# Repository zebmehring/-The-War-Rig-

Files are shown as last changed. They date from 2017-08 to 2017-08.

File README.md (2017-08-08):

# -The-War-Rig-

These are the SolidWorks design files and other submitted material for a project in Yale's Undergraduate Mechanical Engineering program (specifically for MENG 185 - Mechanical Design). The project was completed over the course of spring 2016. All files are posted here under fair use and all credit for the assignment and associated administrative files goes to the issuing department.

* tl;dr: I helped build a remote controlled car out of stuff you really shouldn't bother building a remote controlled car out of. But it drove pretty ok, I guess.

The goal of the project was to construct a remote-controlled vehicle using laser-cut delrin, aluminum rod, plastic gears, toy-car-like-tires, and 3 motors from power screwdrivers. It underwent testing on an obstacle course that involved: pulling a 7kg block of lead up a 45 degree slope, navigating over rough terrain, traversing through a tunnel, making a tight turn, and weaving through a set of cones. Thus, the specifications of dimension, manuverability, and power were had to be optimized for. For example, plenty of torque could be achieved with the maximum number of motors and gears, but this constrained the vehicle in other capacities. Materials were a constrained variable--a specified budget for gears, number of motors and wheels, and supply of rod and delrin could be used in the final design. Calculations were done to ensure correct gear ratio for proper torque, ideal dimensions for combating obstacles, and other variables.

Overall the project was a success--"The War Rig" was able to complete all obstacles save the block towing (this specification was later concluded to be unfair for the power of the motors which were given in the year the experiment was conducted--even with 3 forward-facing motors and optimal gear ratios, this was a challenging feat). It came out second overall in terms of raw performance in the class.

My personal contributions include: designing the chassis to maximize stability while conforming to dimensional constraints (yes it looks goofy, but it works!), designing external set of chassis walls to protect the gear train and stabilize the axles (taking the vehicle from immobile to driving), testing the power of the motors and calculating the appropriate gear ratios to achieve estimated power, much machining and finagling to get parts to fit together, and writing the majority of the final report.

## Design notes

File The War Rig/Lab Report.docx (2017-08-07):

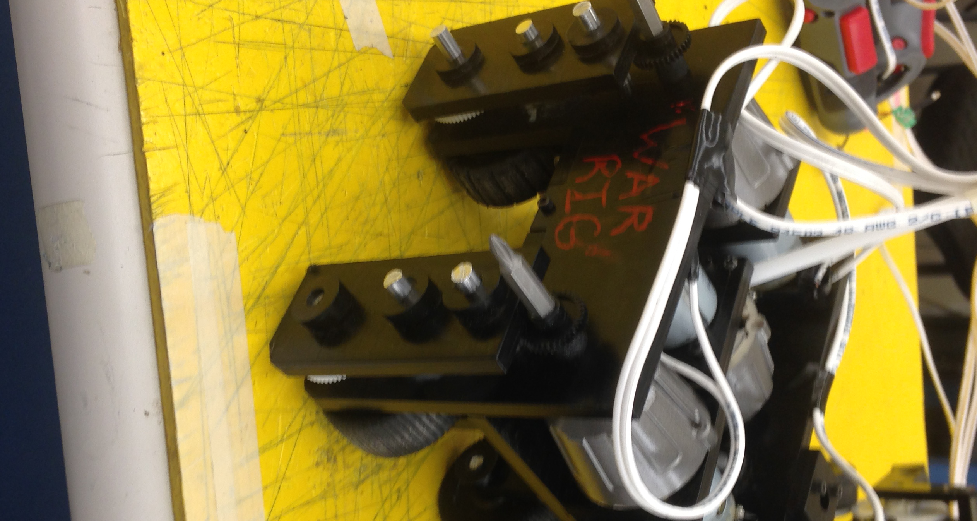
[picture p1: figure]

Lab #3 – ATV

T1—“War Rig”

Sierra Jackson, Stuart Monk, Zeb Mehring

MENG 185: Mechanical Design

10 May 2016

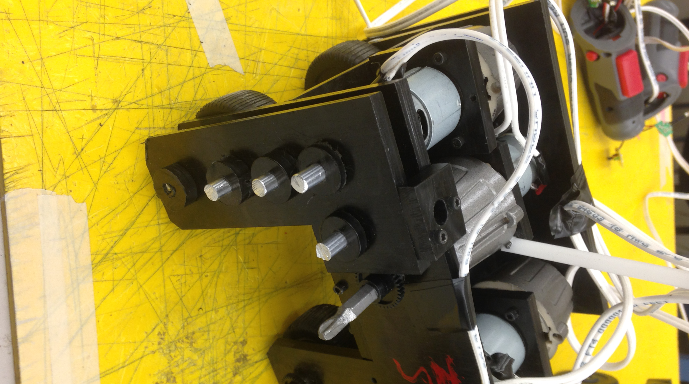
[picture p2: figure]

Overview:

The ultimate objective of this lab was to build an ATV capable of traversing a pre-specified obstacle course. To construct it, we were given three power screwdrivers, a sheet of Delrin (equivalent to 12x12” in surface area), three feet of a .25” diameter aluminum rod, wheels, screws, and $80 with which to purchase plastic gears.

Our approach was to create a three-wheeled vehicle driven by all three motors from the power screwdrivers. The steering is differential: it is accomplished by modulating the turning of the front motors by the driver. The gear ratio was calculated based off of the estimated necessary torque increase, and idle gears were added to raise the chassis base and increase the undercarriage clearance. A combination of screws and “puzzle geometry” were used to lock the chassis into place, while axles held between two or three supporting walls served as mounts for the gears and wheels. The wheels were given treads to increase traction and because treads (along with the battle spikes a.k.a. drill bits) look awesome.

The goals for this design were: to create a vehicle that could provide a high torque (we erred on the side of completing the course rather than going for record-times), to make a simple steering system that did not rely on the proper operation of a single motor and its gear train, to minimize the total volume occupied by the vehicle to increase the error margin resultant from the driver, and to build a model that would be sturdy enough to withstand multiple bouts of practice and competition. The final product, though it veered from the ideal conceptual design, achieved most of these goals.

Design Specifications:

Specification | Dimension
Mass | 1.8 kg
Undercarriage Clearance | 3.2 cm
Turning Radius | 11.4 cm
Drive Train Gear Ratio | 162 (each of 3 motors)
Steering Gear Ratio | 162
No Load Horizontal Speed | 7.6 cm/s
Peak Power | 20 W
Towing Capacity | 27 N

Evaluation:

Several of our goals were happily exceeded by our car. Our turning radius in practice was phenomenally small, as we did not anticipate being able to drag the rear wheel train without driving it (a feat of which the final product was capable). Our car was also perfectly sized despite the addition of drill bits to mount the pinion gears which increased the width by about an inch. Although ground clearance was a theorized issue, our car managed to overcome every obstacle without noticeable problems. We were able to hitch the trailer and drag it up the modified ramp with ease, and we were also able to drive our vehicle (perhaps better than forwards) backwards.

Certain other goals were not met to our full satisfaction, mostly design (as opposed to performance) related ones. We were never able to fully solve a gear meshing issue on our second motor’s gear train which inhibited the maximum torque our car could produce. Similarly, a strange weight imbalance caused issues with creating enough normal force on that same wheel for ideal torque production. More generally, our design failed to be as simple as we had originally envisioned. With many axles and attachment points, a big flaw in our design turned out to be the need to assemble everything at once (which was very difficult). Furthermore, editing the assembled car was difficult and disheartening because of this fact.

If we were to begin from scratch, we would have optimized our design and assembly processes in several ways. Firstly, we would have designed keeping assembly in mind, to eliminate the problems caused by having to put everything together at once and by having to deconstruct the entire model to repair the motors. We would have also looked for a more precise way to mount our gears to improve meshing. Finally, we would have implemented features like a fourth wheel, the inner wheel mounts, and the motor mounts much earlier on in the process. This being said, our overall design would not be altered significantly.

Process:

We began with an in-class brainstorming session which spawned numerous options for our design—four wheels vs. three wheels, two driving motors vs. three driving motors, shared wheel axles vs. single wheel axles, etc.—but we initially settled on a three-wheeled, three-motor layout. This design was chosen because it was the simplest (in theory), had an uncomplicated steering mechanism, conferred decent agility, and could be compacted into a small space to better traverse the obstacle course.

From this idea, we created a foam core model. It had two steering wheels at the front controlled by two separate motors driving different gear trains of equal gear ratio. The back wheel was placed in a Delrin box which was connected axially to a motor which would allow it to pivot. All three motors were housed laterally in a box-shaped chassis with significant ground clearance.

Upon review and discussion, we modified several aspects of this design to better suit our goals for the project. Because we were advised that the “rudder” pivot wheel would not greatly contribute to the steering of the ATV, we instead converted it into a static wheel driven straight forward by the third motor. This increased our overall torque in exchange for a small advantage in turning (now the differential system would have to overcome the friction of a sliding back wheel). As a result, the back axle became a much simpler system. Also addressed was a stability issue: lack of dual axle support. We added in external support walls to give each axle two bases to balance on and to protect the gears from bumping into the course as a result of reckless driving. Finally, the driving wheels were placed underneath the chassis instead of outside of it, reducing the total width of the vehicle by at least two inches.

Further nuance was added in the CAD phase, which involved creating every part on SolidWorks. Each group member worked on a different part of the vehicle, adding the proper dimensions, shaft holes, and other features based on the measurements taken from the motors and the restrictions imposed by the obstacle course. In addition to our foam core model, we added dovetails to select pieces of the chassis to increase stability and also specified the sites on the design where we wanted to insert screws (by using a quick burst of heat from the laser cutter). We also added motor mounts in this phase to secure the motors to the chassis even more tightly. Each group member then worked on different subassemblies (wheel axles, chassis, gear trains, etc.) until all the constituent pieces were ready to assemble the final design. Mates were quickly added and we cycled through turns creating the final in-context screw holes before submitting the assembly for cutting.

With all the materials in hand, we proceeded to machine and assemble the model. Using the drill press, we tapped all the necessary screw holes. The hacksaw was used to create axle bits of specified length and the bandsaw was used to tread the wheels. The lathe was used to machine the axle caps. As finalized pieces became available, we used the arbor press to press-fit axle caps, gears, and wheels onto their respective shafts, which then became locked to the chassis (occasionally having to drill through the shaft and use small pins to secure the fit). After a complex analysis of which parts to secure first, we proceeded to screw everything into place. Throughout this process, countless subassemblies were made to ensure that the parts interfaced, and many times small corrections had to be made. As a result, it was much less methodical than depicted here.

The tweaking and repair process consisted mainly of: disassembling the car to repair the motors, attempting to increase the weight on the starboard side of the car to give the second wheel traction, screwing on makeshift supports to mesh the second gear train better, and test driving the car to make sure that everything was working harmoniously.

After much toil, the car eventually drove neatly and was able to accomplish many of the goals we had in mind. Coincidentally, these pieces finally came together just before the deadline, so no further attempts to fix non-critical issues were able to be made.

Time Log:

Activity | Person Hours
Conceptual Development | 12
SolidWorks | 18
Milling | 102
Assembly | 30
Repair and Redesign | 24
Evaluation | 4
Total | 190

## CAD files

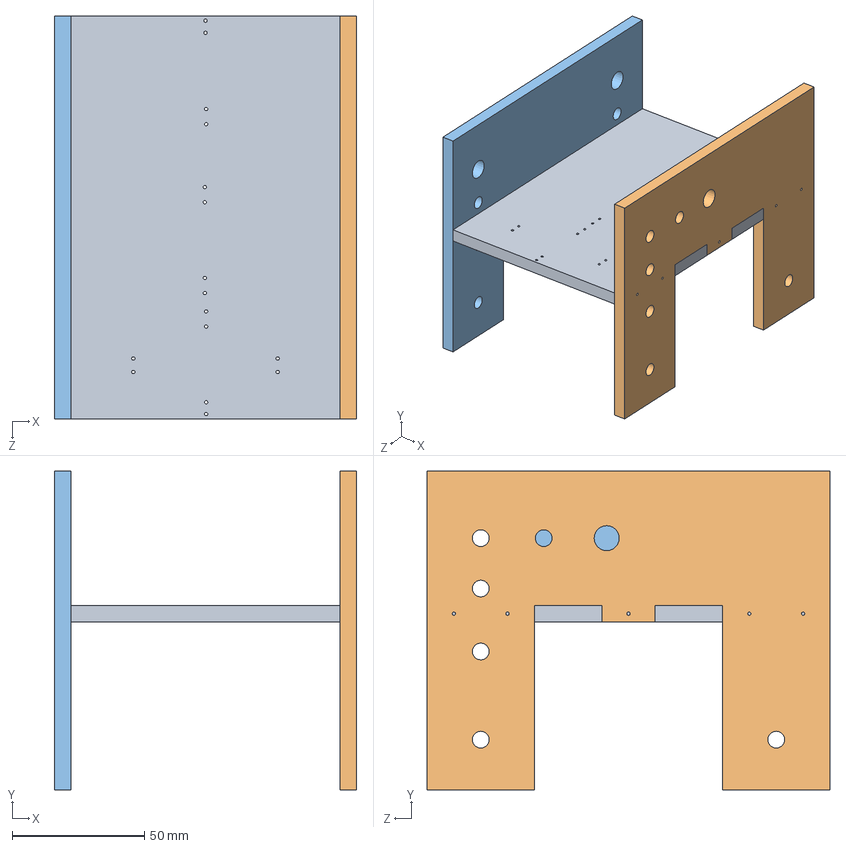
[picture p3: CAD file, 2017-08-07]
The War Rig/Sierra, Stuart, Zeb Car Parts/Assemblies/JMM-Chassis_Assembly.SLDASM
114.3 x 120.7 x 152.4 mm
Base_Plate
Side_Plate (1M)
Side_Plate (2M)

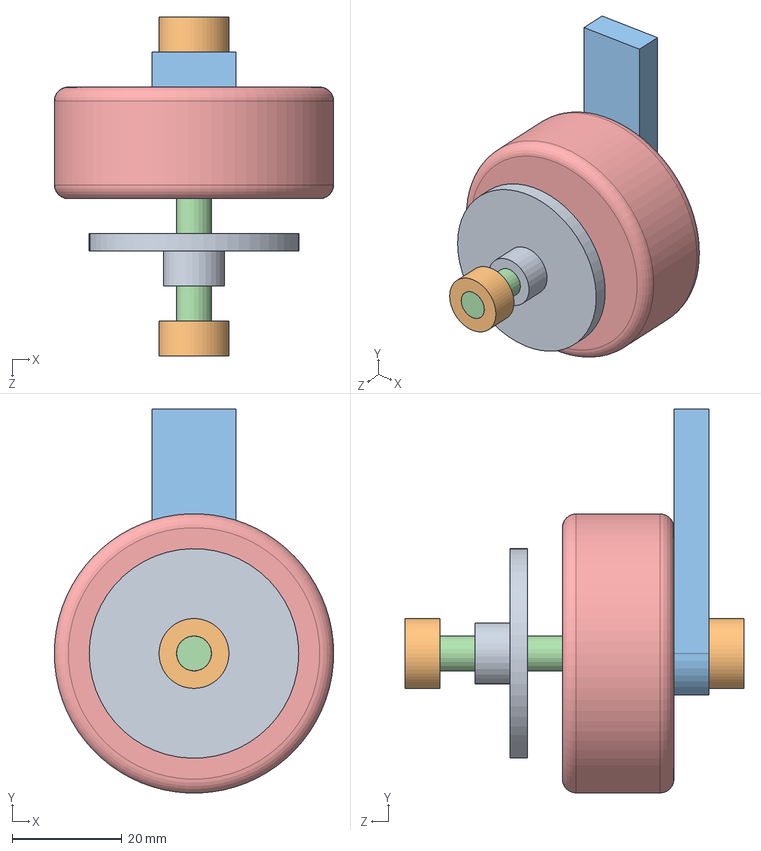
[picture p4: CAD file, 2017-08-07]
The War Rig/Sierra, Stuart, Zeb Car Parts/Assemblies/JMM-Front Wheel Assembly.SLDASM
50.8 x 69.8 x 61.6 mm
72-Gear
Axel Washer x 2
Front Wheel Support
Front Wheels Axel
Wheel

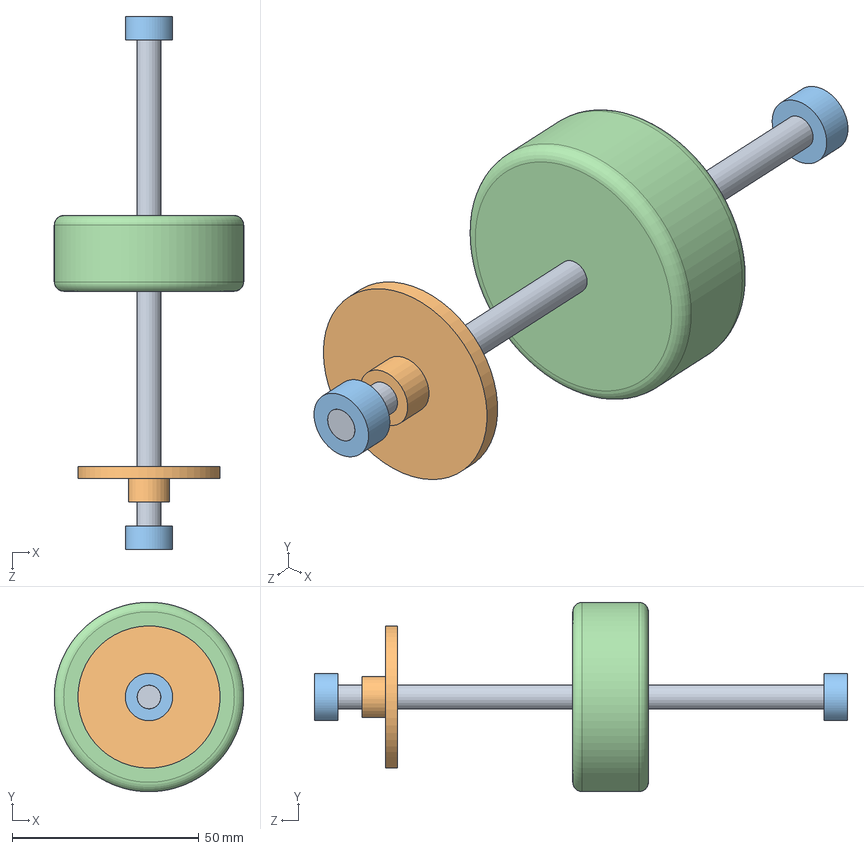
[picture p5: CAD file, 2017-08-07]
The War Rig/Sierra, Stuart, Zeb Car Parts/Assemblies/JMM-Back Wheel Assembly.SLDASM
50.8 x 50.8 x 142.9 mm
Back Axel
72-Gear
Axel Washer x 2
Wheel

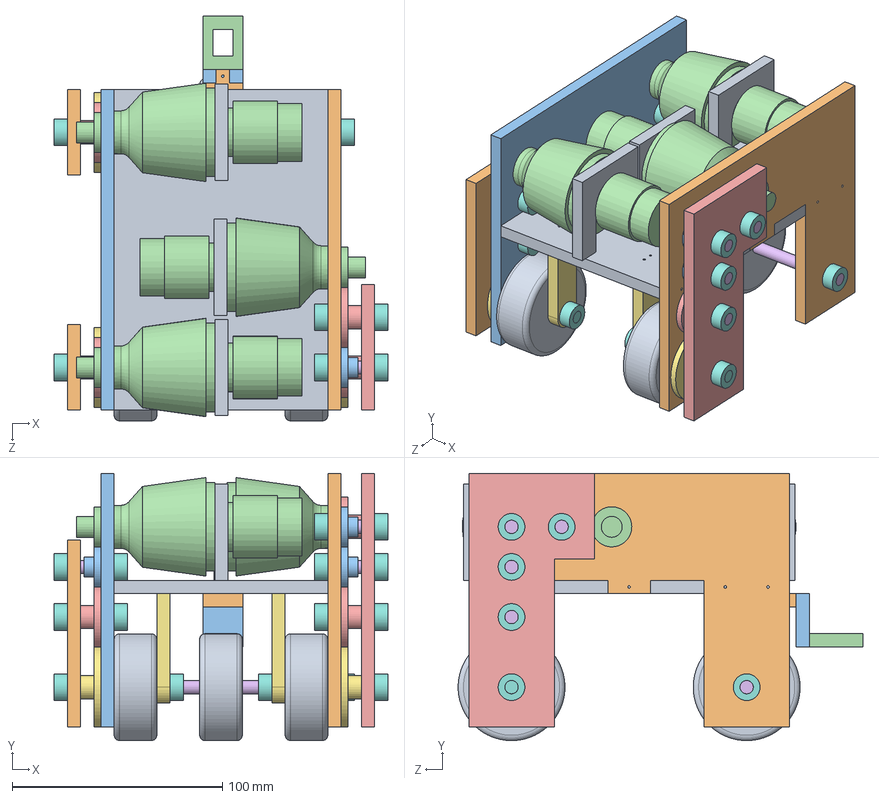
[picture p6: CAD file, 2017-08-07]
The War Rig/Sierra, Stuart, Zeb Car Parts/Assemblies/JMM-Car_Assembly.SLDASM
158.8 x 127.0 x 192.4 mm
Base_Plate
Side_Plate (1M)
Side_Plate (2M)
motor x 3
L_Gear_Cover_Plate
Back Axel
72-Gear x 3
Axel Washer x 22
Wheel x 3
Straight_Gear_Cover_Plate x 2
36-Gear x 4
36-Gear for Engine x 3
54-Gear x 4
Train Axel x 8
Front Wheel Support x 2
Front Wheels Axel x 2
Motor_Support x 3
Trailer_Arm_H
Trailer_Arm_V
Trailer_Hook

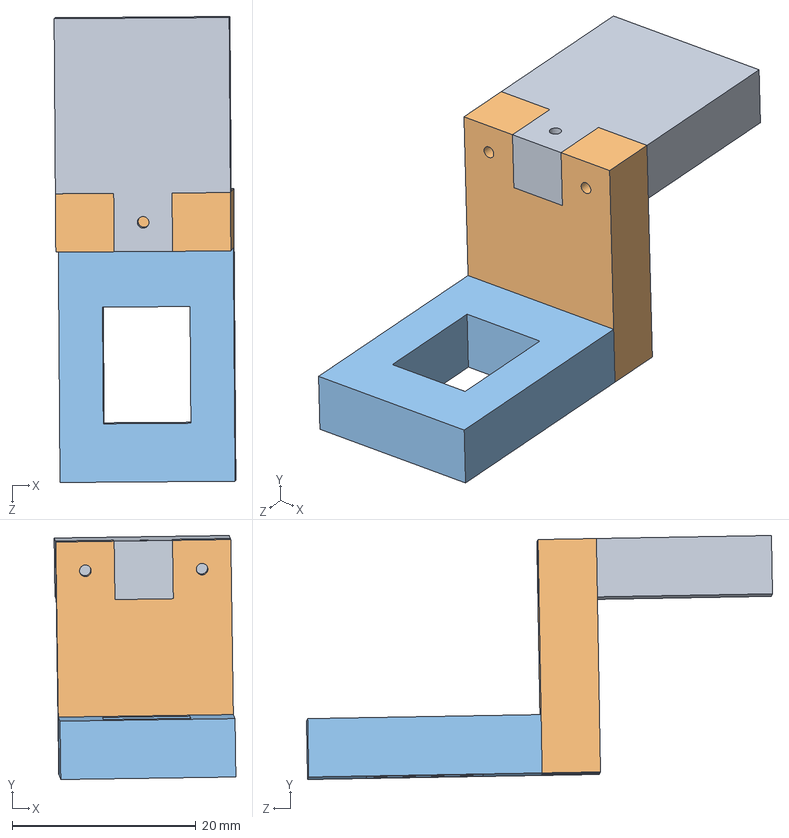
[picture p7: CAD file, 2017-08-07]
The War Rig/Sierra, Stuart, Zeb Car Parts/Assemblies/JMM-Trailer Hitch.SLDASM
19.8 x 26.6 x 50.7 mm
Trailer_Arm_H
Trailer_Arm_V
Trailer_Hook

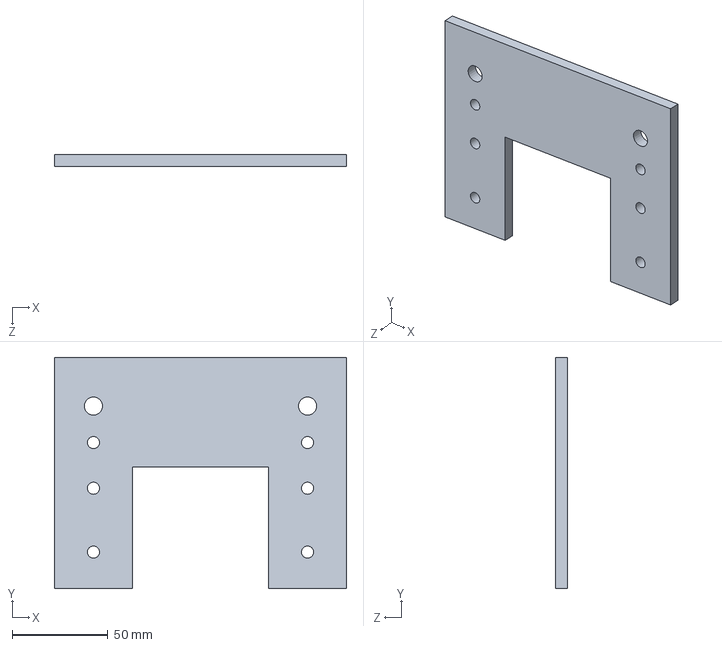
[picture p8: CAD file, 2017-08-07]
The War Rig/Sierra, Stuart, Zeb Car Parts/Parts/JMM-Side Plate (2M).SLDPRT
152.4 x 120.7 x 6.35 mm

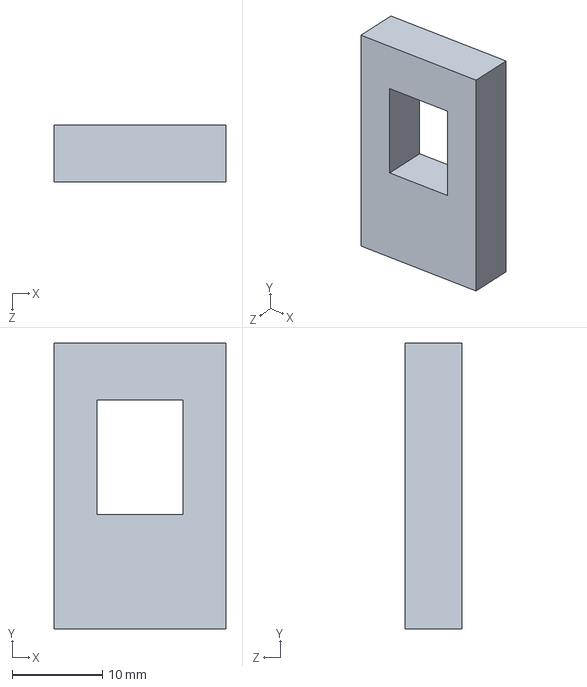
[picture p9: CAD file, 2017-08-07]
The War Rig/Sierra, Stuart, Zeb Car Parts/Parts/JMM-Trailer Hook.SLDPRT
19.1 x 31.8 x 6.35 mm

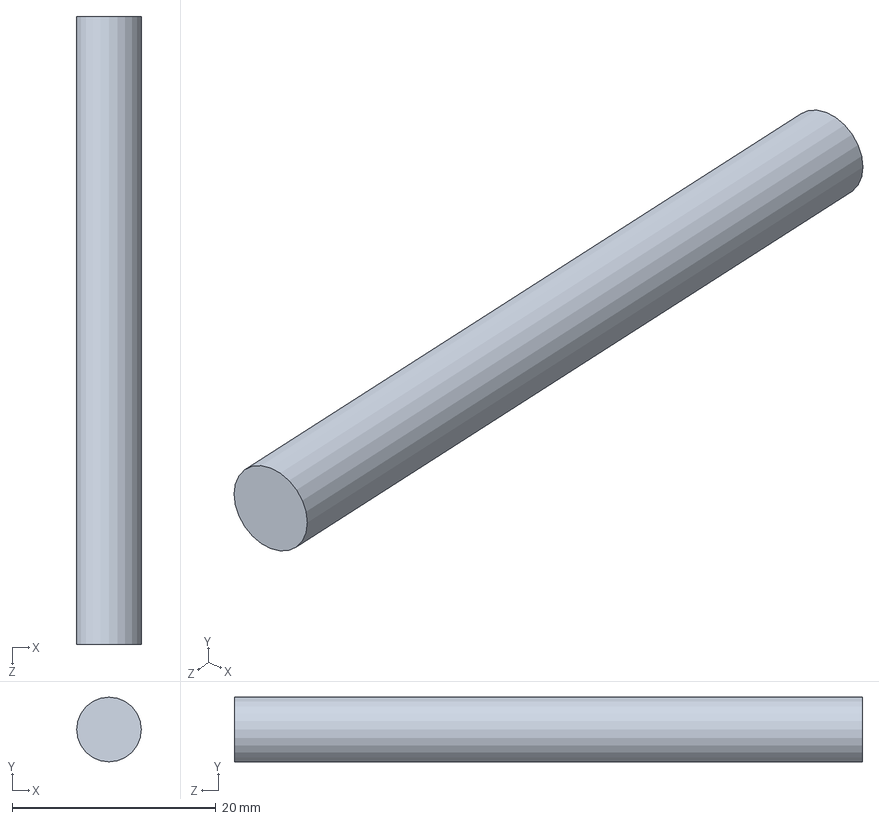
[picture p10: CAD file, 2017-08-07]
The War Rig/Sierra, Stuart, Zeb Car Parts/Parts/JMM-Front Wheels Axel.SLDPRT
6.35 x 6.35 x 61.6 mm

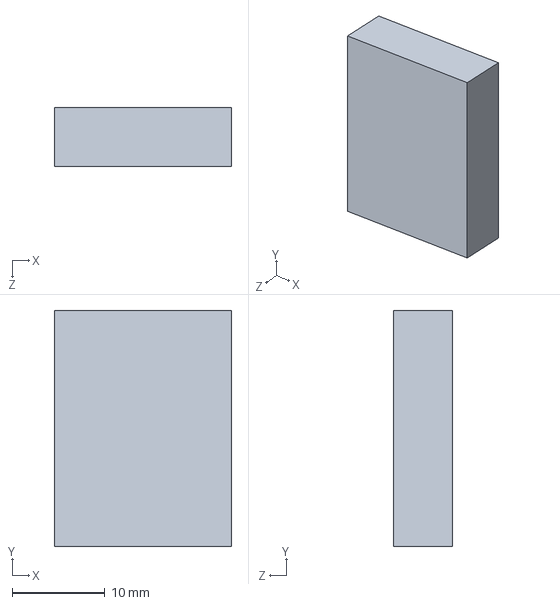
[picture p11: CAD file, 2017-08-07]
The War Rig/Sierra, Stuart, Zeb Car Parts/Parts/JMM-Trailer Arm V.SLDPRT
19.1 x 25.4 x 6.35 mm

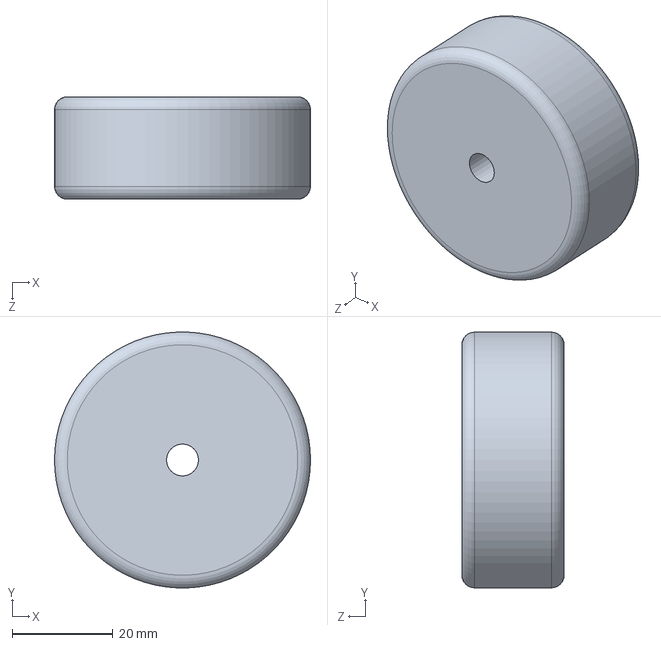
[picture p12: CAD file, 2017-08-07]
The War Rig/Sierra, Stuart, Zeb Car Parts/Parts/JMM-Wheel.SLDPRT
50.8 x 50.8 x 20.3 mm

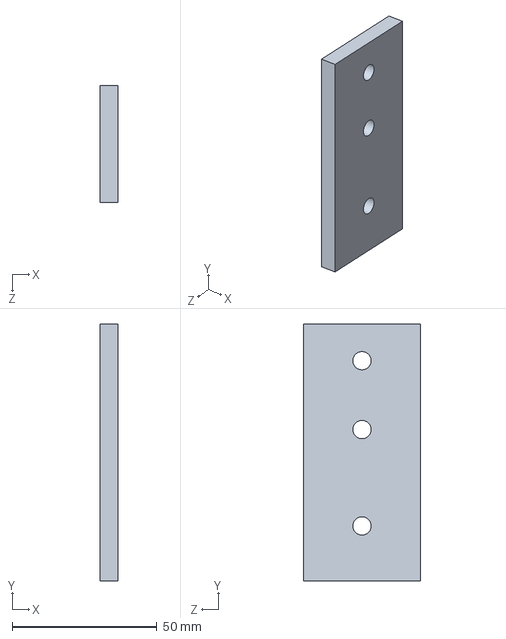
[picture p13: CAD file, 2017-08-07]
The War Rig/Sierra, Stuart, Zeb Car Parts/Parts/JMM-Straight Gear Cover Plate.SLDPRT
6.35 x 88.9 x 40.6 mm

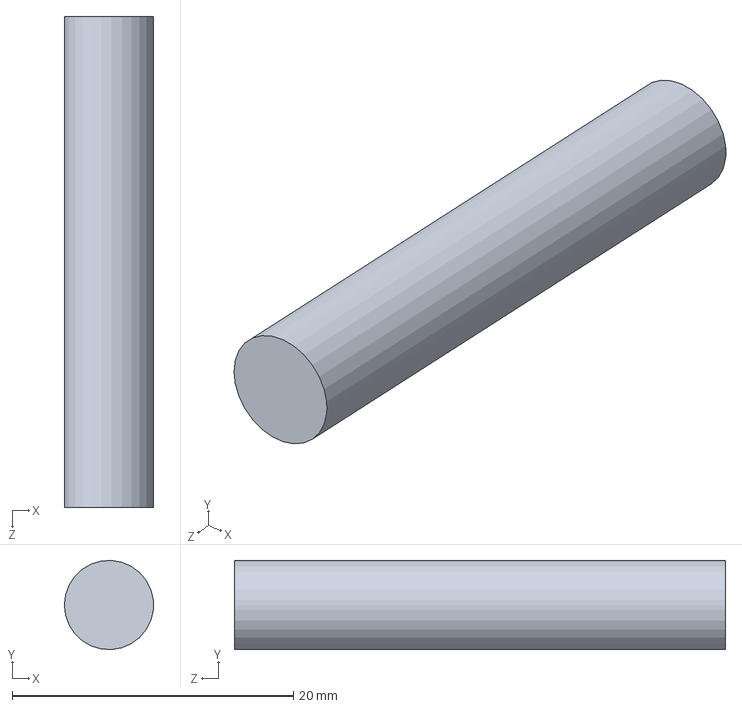
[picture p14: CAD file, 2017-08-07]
The War Rig/Sierra, Stuart, Zeb Car Parts/Parts/JMM-Train Axel.SLDPRT
6.35 x 6.34 x 34.9 mm

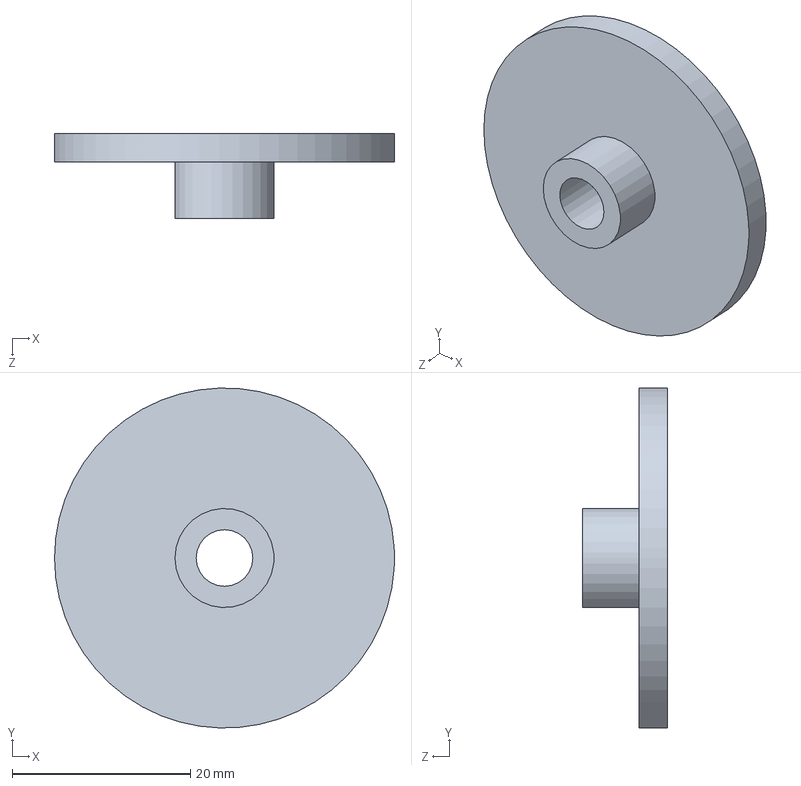
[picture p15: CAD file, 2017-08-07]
The War Rig/Sierra, Stuart, Zeb Car Parts/Parts/JMM-72 Gear.SLDPRT
38.1 x 38.1 x 9.53 mm

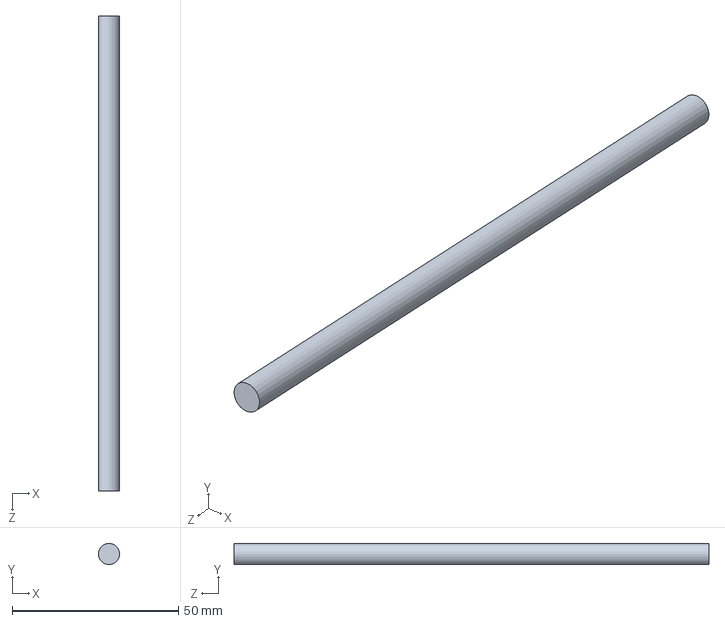
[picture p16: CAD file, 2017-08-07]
The War Rig/Sierra, Stuart, Zeb Car Parts/Parts/JMM-Back Axel.SLDPRT
6.35 x 6.35 x 142.9 mm

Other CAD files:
The War Rig/Sierra, Stuart, Zeb Car Parts/Parts/JMM-Side Plate (1M).SLDPRT
The War Rig/Sierra, Stuart, Zeb Car Parts/Parts/JMM-36 Gear for Engine.SLDPRT
The War Rig/Sierra, Stuart, Zeb Car Parts/Parts/JMM-Trailer Arm H.SLDPRT
The War Rig/Sierra, Stuart, Zeb Car Parts/Parts/JMM-L Shaped Gear Cover Plate.SLDPRT
The War Rig/Sierra, Stuart, Zeb Car Parts/Assemblies/JMM-Washer for Train Axle.SLDASM
The War Rig/Sierra, Stuart, Zeb Car Parts/Parts/JMM-36 Gear.SLDPRT
The War Rig/Sierra, Stuart, Zeb Car Parts/Parts/JMM-54 Gear.SLDPRT
The War Rig/Sierra, Stuart, Zeb Car Parts/Parts/JMM-Axel Washer.SLDPRT
The War Rig/Sierra, Stuart, Zeb Car Parts/Parts/JMM-Base Plate.SLDPRT
The War Rig/Sierra, Stuart, Zeb Car Parts/Parts/JMM-Front Wheel Support.SLDPRT
The War Rig/Sierra, Stuart, Zeb Car Parts/Parts/JMM-Motor Model.SLDPRT
The War Rig/Sierra, Stuart, Zeb Car Parts/Parts/JMM-Motor Support.SLDPRT
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

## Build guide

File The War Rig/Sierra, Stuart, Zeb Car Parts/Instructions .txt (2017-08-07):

For our car we need one cut of every part other than the ones listed below. Those require the number of cuts specified.

We could not tell from the lab handout if we would be given the end caps which press fit to hold our axels in place.

We made our own called Washer for Train Axle and will need 22 cuts if there are no other form of end cap provided. 

Straight Gear Cover Plate  2 cuts

Front Wheel Support 2 Cuts

Motor Support  3 cuts

Washer for Train Axle  22 cuts (seen note above)
